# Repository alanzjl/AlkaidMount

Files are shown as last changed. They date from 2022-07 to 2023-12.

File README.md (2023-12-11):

# Alkaid Mount - DIY Equatorial Mount with HarmonicDrive

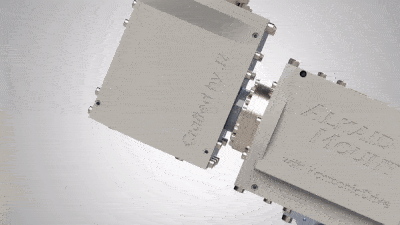
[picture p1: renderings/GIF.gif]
rendering


Built by JZ.

For my build log, checkout [this page on my website](https://alanz.info/pages/alkaidmount.html).

The following YouTube video documents all the processes with no explaination:
Youtube Video (https://www.youtube.com/watch?v=k2GoMa2DpH8)

The same video can also be found on [bilibili](https://www.bilibili.com/video/BV1SR4y1X7bt/?share_source=copy_web&vd_source=4d6f936f693563e28752aadac9dd326f).

- Note: do not directly use the dxf files under the Machine/ folder.
They are for reference only and they might contain duplicated parts, because I had to make several parts more than once due to some mistakes at the beginning.
I'd recommend looking at the solidworks files first and try to understand every part, then generate your own dxf.

## Introduction
AlkaidMount is a DIY aluminum HarmonicDrive German style equatorial mount with a ~25lbs unbalanced or >70lbs balanced load capacity, with a self weight of only ~16lbs.
Each axis consists of a 100:1 HarmonicDrive gearbox, followed by a 27:1 planetary gearbox, driven by a Nema17 stepper motor.

Weight capacity is calculated with gearbox load limits as well as rigid body simulation.
Note that I have not yet done any torture tests, so those numbers are all theoratical. 
I've only tested it on the two scopes I own - an unbalanced Williams Optics GT71 setup (~15lbs) and balanced a Meade LX200 8" SCT setup (~25lbs not including the counterweights).
Both setups worked beautifully.

This repo contains ALL the design files (CAD, manufacture drawings, PCB files, software) to make the AlkaidMount.
I made this repo public to inspire other ideas.
Due to the difficulty in sourcing the exact same model of the two HarmonicDrive's (unless you buy new:), replicating the exact same mount would be hard. 
However modifying this design to suite other HD models shouldn't be too hard.

## BOM - Hardware
-----------
| Name | Quantity | Drawings | Datasheet |
| --- | --- | --- | --- |
| Harmonic Drive CSF-17-100-2UH-LW | 2 | [Drawings](https://www.harmonicdrive.net/_hd/content/caddownloads/dxf/csf-2uh_gearheads/csf-17-xx-2uh.pdf) | [Datasheet](https://www.harmonicdrive.net/products/gear-units/gear-units/csf-2uh/csf-17-100-2uh) |
| Nema 17 with 27:1 Planetary Gearbox | 2 | [Drawings](https://www.omc-stepperonline.com/download/17HS19-1684S-PG27.pdf) | [Datasheet](https://www.omc-stepperonline.com/nema-17-stepper-motor-bipolar-l-48mm-w-gear-ratio-27-1-planetary-gearbox-17hs19-1684s-pg27) |
| 1/8" Aluminum plate | 12"x12" minimum | - | - |
| 1/4" Aluminum plate | - | - | - |
| M4x8 | many :) | - | - |
| M3x8 | not that many :] | - | - |
| M5x8 | a few :{ | - | - |

## BOM - Electronics
-----------
| Name | Quantity | Drawings | Datasheet |
| --- | --- | --- | --- |
| Teensy 4.0 | 1 | - | - |
| ESP-32 (for wifi control) | 1 | - | - |

For parts on the PCB, see [PCB/parts.txt](PCB/parts.txt).

## Manufacturing guide

Most parts were made with 2D waterjetting, with not too much post-processing (tab removal, tapping if needed).
Some parts have holes on the side, so some milling was involved.

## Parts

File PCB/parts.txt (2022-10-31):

Partlist

Exported from untitled.sch at 10/31/2022 12:25 AM

EAGLE Version 9.6.2 Copyright (c) 1988-2020 Autodesk, Inc.

Assembly variant: 

Part     Value          Device                             Package                                   Library                            Sheet

5V_REG   TSR_5V         TSR_5V                             TSR_5V                                    alans_lbr                          1
AUX3                    PINHD-1X2                          1X02                                      pinhead                            1
AUX4                    PINHD-1X2                          1X02                                      pinhead                            1
C1       0.33uF         C-EU050-024X044                    C050-024X044                              rcl                                1
C2       100uF          CPOL-EUE5-8.5                      E5-8,5                                    rcl                                1
C3       0.1uF          C-EU050-024X044                    C050-024X044                              rcl                                1
C4       47uF           CPOL-EUE5-8.5                      E5-8,5                                    rcl                                1
C5       0.1uF          C-EU050-024X044                    C050-024X044                              rcl                                1
C6       47uF           CPOL-EUE5-8.5                      E5-8,5                                    rcl                                1
C7       100uF          CPOL-EUE5-8.5                      E5-8,5                                    rcl                                1
D1       1N4004         1N4004                             DO41-10                                   adafruit                           1
FUSE1    5X20MM_FUSE    5X20MM_FUSE                        5X20MM_FUSE                               alans_lbr                          1
HND      RJ11-4X        RJ11-4X                            RJ11-NO_SHIELD                            con-tycoelectronics                1
HND_5V                  PINHD-1X2                          1X02                                      pinhead                            1
J1                      DCJ0303                            DCJ0303                                   con-jack                           1
LED1                    LED5MM                             LED5MM                                    adafruit                           1
LED2                    LED5MM                             LED5MM                                    adafruit                           1
LED3                    LED5MM                             LED5MM                                    adafruit                           1
PEC                     PINHD-1X2                          1X02                                      pinhead                            1
R1       4.7k           R-EU_0207/7                        0207/7                                    rcl                                1
R2       2k             R-EU_0207/7                        0207/7                                    rcl                                1
R3       2k             R-EU_0207/7                        0207/7                                    rcl                                1
R4       2k             R-EU_0207/7                        0207/7                                    rcl                                1
R5       2k             R-EU_0207/7                        0207/7                                    rcl                                1
R6       3.3k           R-EU_0207/7                        0207/7                                    rcl                                1
R7       3.3k           R-EU_0207/7                        0207/7                                    rcl                                1
R8       10k            R-EU_0207/7                        0207/7                                    rcl                                1
R9       10k            R-EU_0207/7                        0207/7                                    rcl                                1
R10      10k            R-EU_0207/7                        0207/7                                    rcl                                1
SWITCH   1X2-3.5MM      1X2-3.5MM                          1X2-3.5MM                                 adafruit                           1
U$1      TEENSY_4.0     TEENSY_4.0                         TEENSY_4.0                                TEENSY 4.0                         1
U1       A4988 etc      A4988_STEPPER_MOTOR_DRIVER_CARRIER MODULE_A4988_STEPPER_MOTOR_DRIVER_CARRIER A4988_STEPPER_MOTOR_DRIVER_CARRIER 1
U2       A4988 etc      A4988_STEPPER_MOTOR_DRIVER_CARRIER MODULE_A4988_STEPPER_MOTOR_DRIVER_CARRIER A4988_STEPPER_MOTOR_DRIVER_CARRIER 1
USB1     USB-B_SOCKET   USB-B_SOCKET                       USB-B_SOCKET                              alans_lbr                          1
X1       USB            JST-XH-04-PIN-ROUND-PAD            JST-XH-04-PACKAGE-ROUND-PAD               JST_XH_Connectors                  1
X2       Axis1          JST-XH-04-PIN-LONG-PAD             JST-XH-04-PACKAGE-LONG-PAD                JST_XH_Connectors                  1
X3       Axis2          JST-XH-04-PIN-LONG-PAD             JST-XH-04-PACKAGE-LONG-PAD                JST_XH_Connectors                  1
X4       WIFI           JST-XH-04-PIN-LONG-PAD             JST-XH-04-PACKAGE-LONG-PAD                JST_XH_Connectors                  1

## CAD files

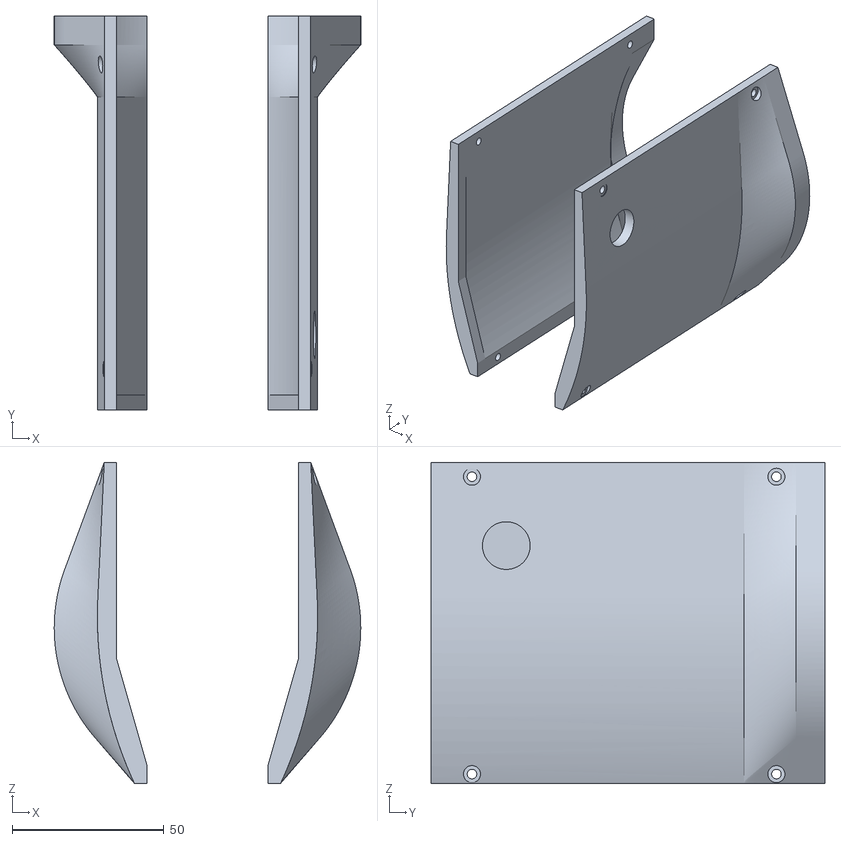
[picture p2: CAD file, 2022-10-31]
CAD/DEC/Part1^DEC_asm.STL
101.0 x 129.8 x 105.9

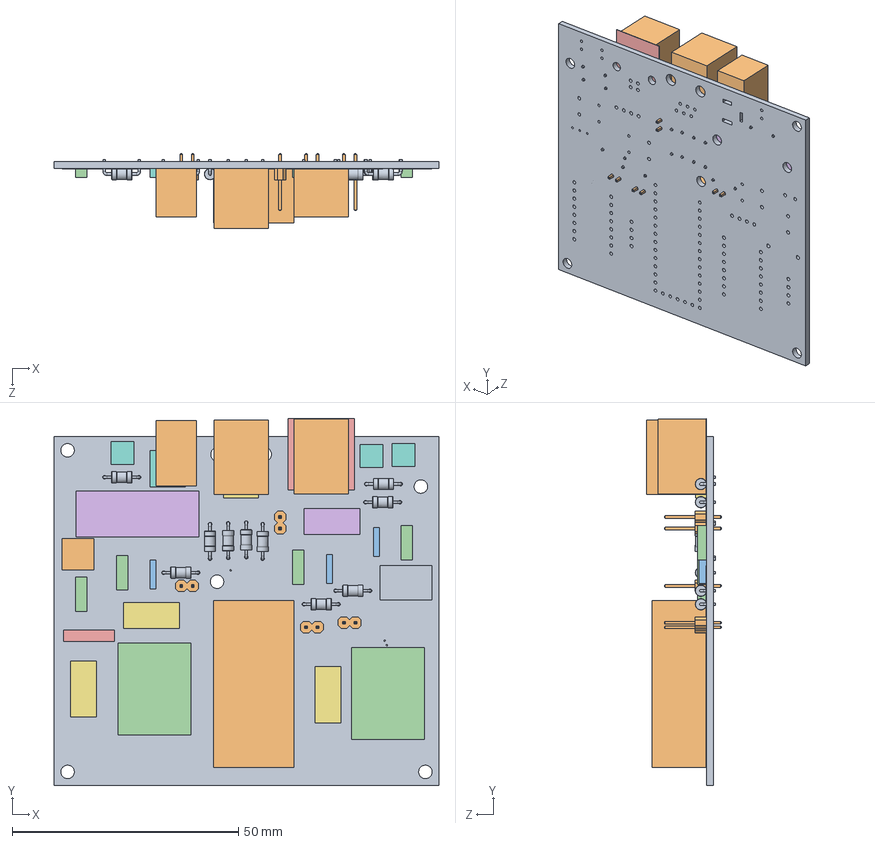
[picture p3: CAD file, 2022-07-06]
CAD/PCB/PCB.SLDASM
85.0 x 81.0 x 16.6 mm
Board.step
1X02.step x 4
0.1uF.step x 3
100uF.step x 4
1N4004.step
5X20MM_FUSE.step
RJ11-4X.step
LED5MM.step x 3
10k.step x 10
1X2-3.5MM.step
TEENSY_4.0.step
A4988 etc.step x 2
USB-B_SOCKET.step
USB.step
WIFI.step x 3
DCJ0303.step
TSR_5V.step
Part37^PCB

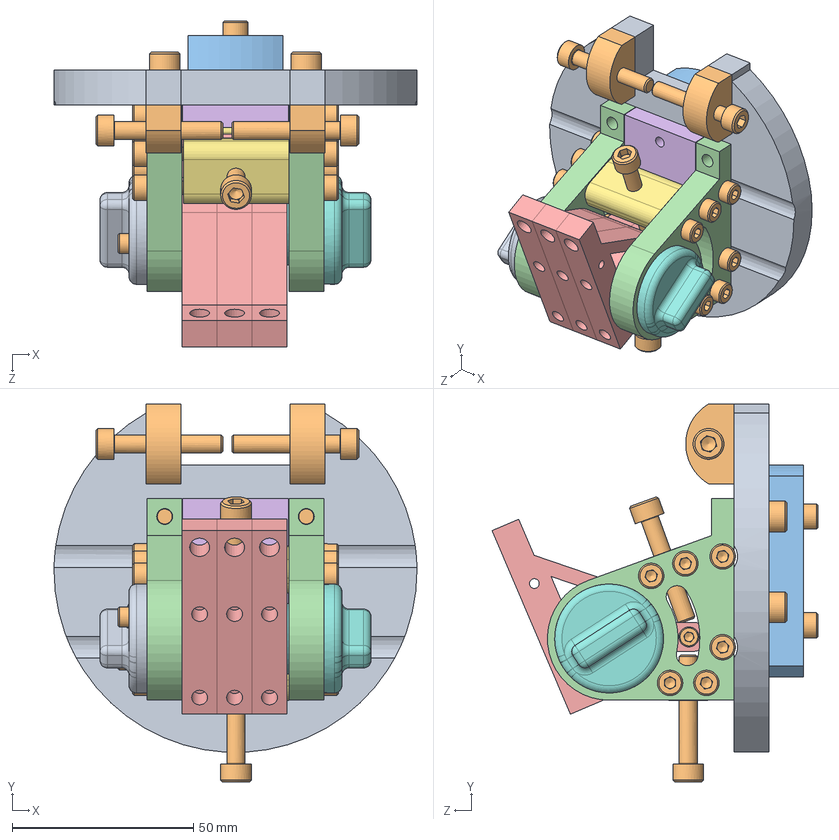
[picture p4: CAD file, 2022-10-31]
CAD/Tangent/tangent_asm.SLDASM
100.0 x 104.1 x 89.8 mm
tangent_base
tangent_az x 2
tangent_tripod_spacer
tangent_alt x 2
tangent_mount x 3
tangent_alt_spacer
alt_bolt_housing x 2
alt_locker_base
alt_locker_cap
socket head cap screw_am x 26
socket countersunk head screw_am x 4

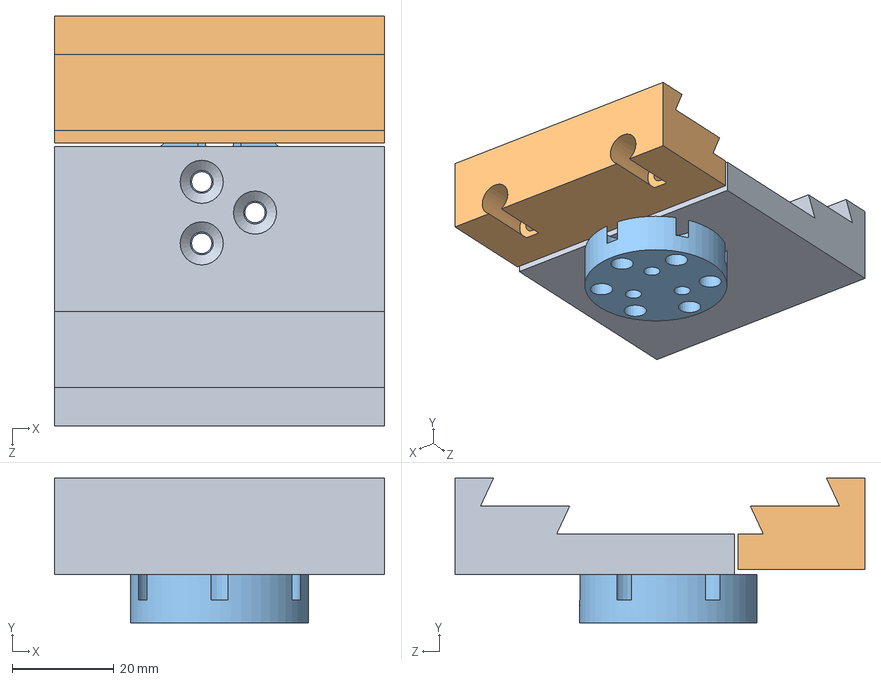
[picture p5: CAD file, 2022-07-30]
CAD/Dovetail/Dovetail_asm.SLDASM
65.0 x 28.5 x 80.7 mm
clamp_main
clamp_side
connector

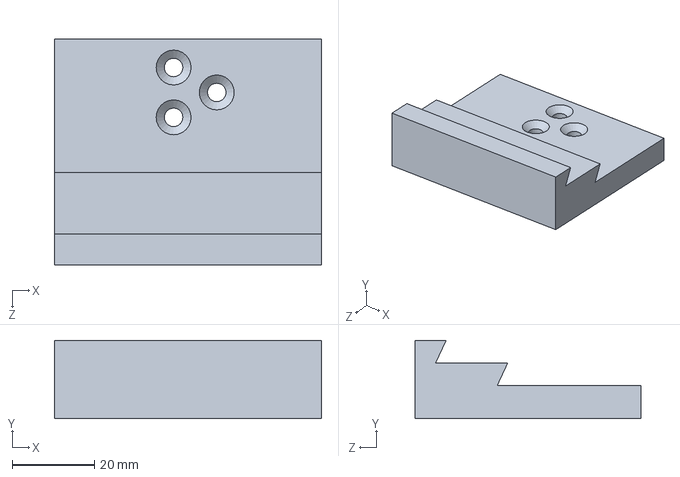
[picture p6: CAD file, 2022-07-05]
CAD/Dovetail/clamp_main.SLDPRT
65.0 x 19.0 x 55.0 mm

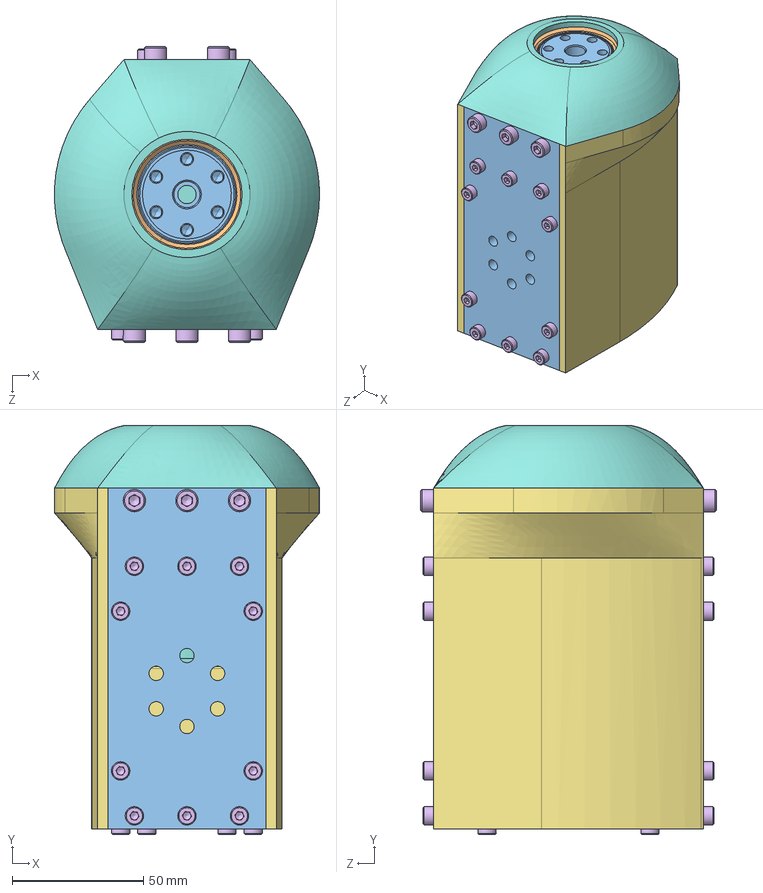
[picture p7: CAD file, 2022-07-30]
CAD/DEC/DEC_asm.SLDASM
100.9 x 155.7 x 112.7 mm
DEC_gearbox_mount
CSF-17-2UH HOUSING.stp
CSF-17-2UH OUTPUT.stp
CSF-17-2A-R OLDHAM COUPLING.stp
1715063_1715063.stp x 2
17 WG BEARING.stp
6627T91_Stepper Motor
Planatary_Gearbox_27_1
DEC_planetary_mount
DEC_top_plate
DEC_bottom_plate
DEC_middle_support_v2
support_triangle x 8
socket head cap screw_am x 33

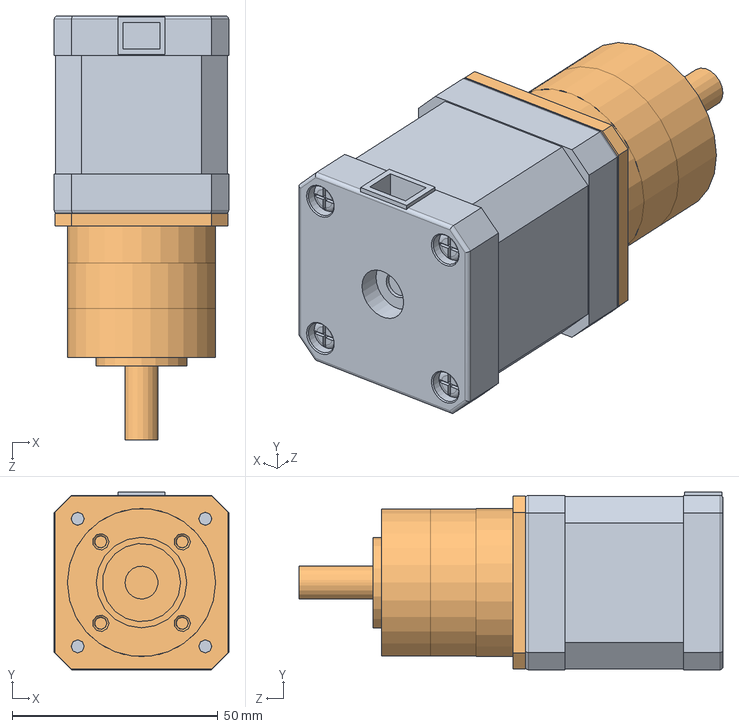
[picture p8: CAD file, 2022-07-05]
CAD/parts/Nema17_27_1.SLDASM
42.4 x 43.2 x 103.0 mm
6627T91_Stepper Motor
Planatary_Gearbox_27_1

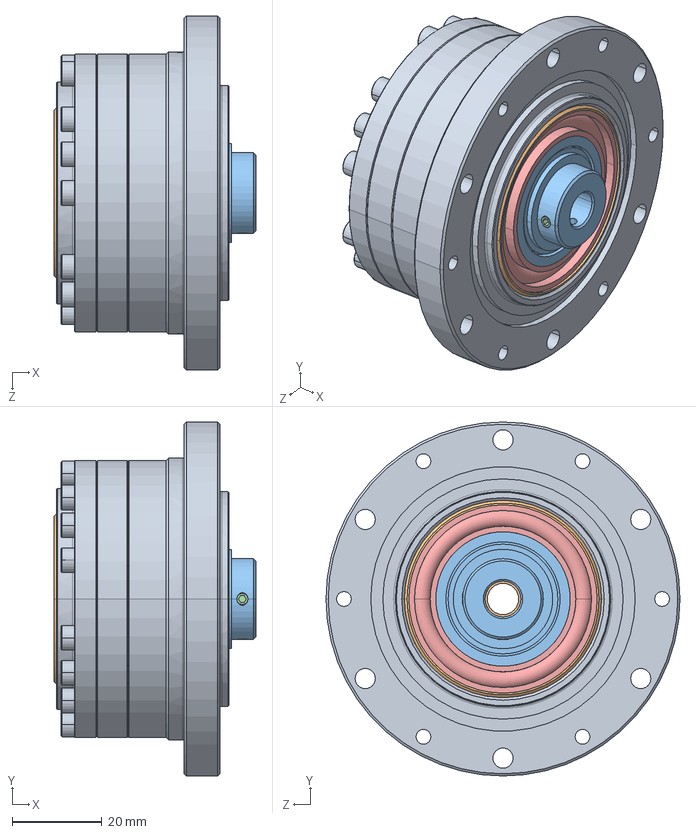
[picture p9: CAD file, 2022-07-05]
CAD/parts/CSF-17-XXX-2UH.stp.SLDASM
45.0 x 79.0 x 79.0 mm
CSF-17-2UH HOUSING.stp
CSF-17-2UH OUTPUT.stp
CSF-17-2A-R OLDHAM COUPLING.stp
1715063_1715063.stp x 2
17 WG BEARING.stp

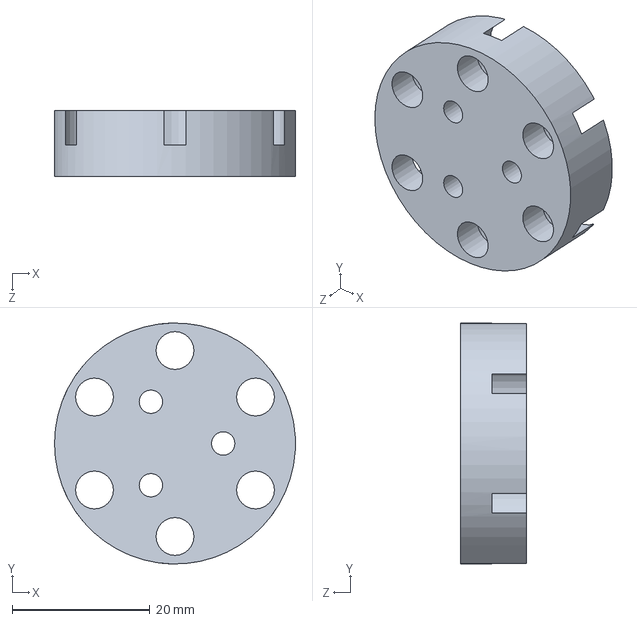
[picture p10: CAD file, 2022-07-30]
CAD/Dovetail/connector.SLDPRT
35.0 x 35.0 x 9.53 mm

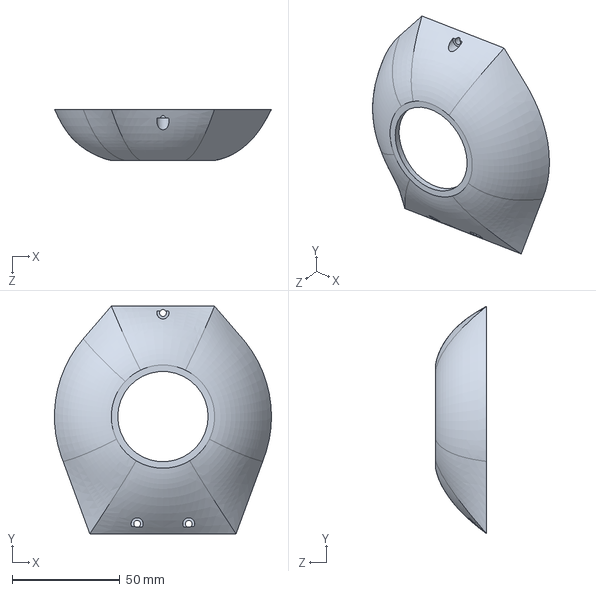
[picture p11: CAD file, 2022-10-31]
CAD/output_cap.SLDPRT
100.9 x 105.9 x 23.8 mm

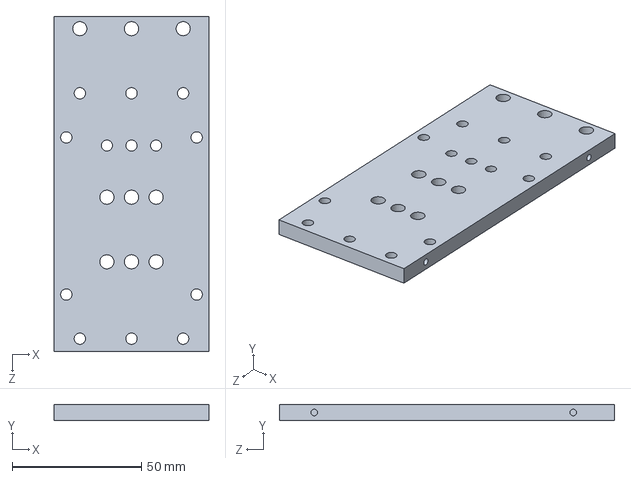
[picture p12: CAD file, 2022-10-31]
CAD/RA/RA_bottom_plate.SLDPRT
60.0 x 6.35 x 129.8 mm

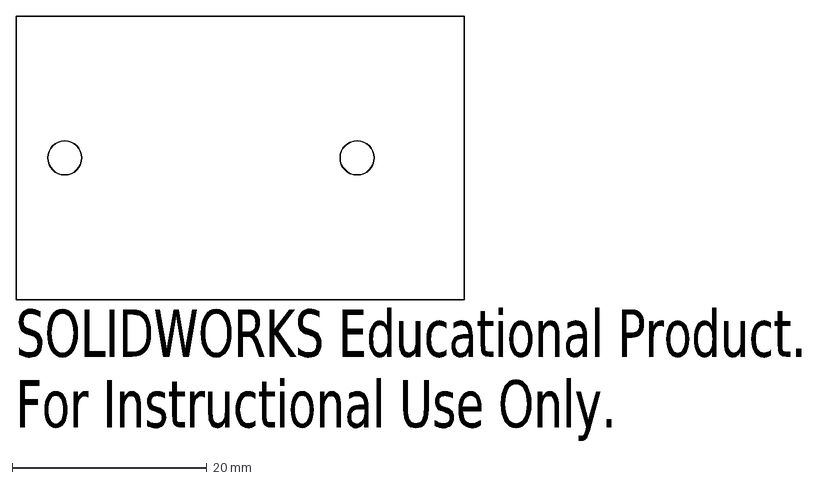
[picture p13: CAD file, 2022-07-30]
Machine/dxf/1_4_inch/1_x_tangent_alt_spacer.DXF
SOLIDWORKS Educational Product.
For Instructional Use Only.

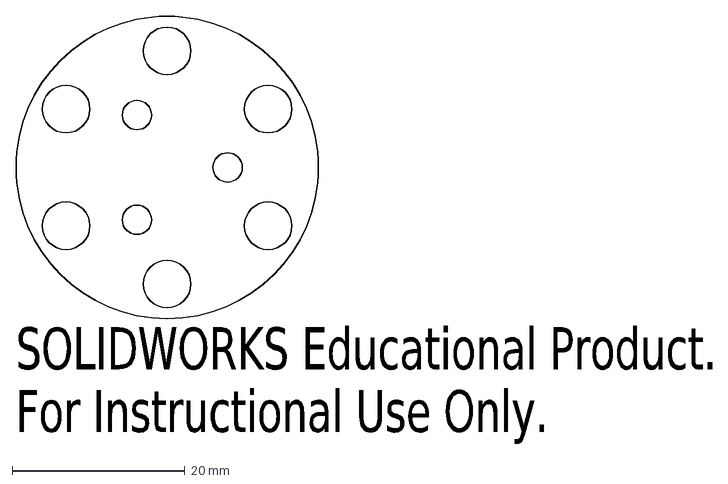
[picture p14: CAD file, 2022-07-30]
Machine/dxf/3_8_inch/1_x_connector.DXF
SOLIDWORKS Educational Product.
For Instructional Use Only.

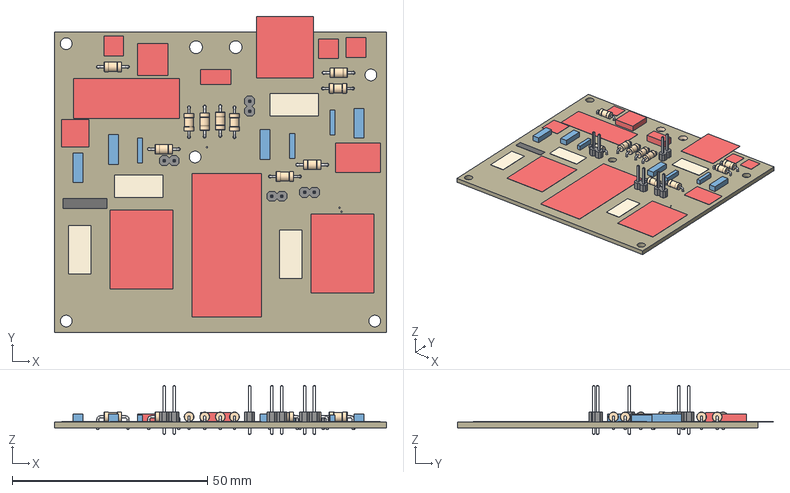
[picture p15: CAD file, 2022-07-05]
CAD/PCB/untitled(2).step
85.0 x 81.0 x 12.6 mm
Board
1X02 x 4
0.1uF x 3
100uF x 4
1N4004
5X20MM_FUSE
RJ11-4X
LED5MM x 3
10k x 10
1X2-3.5MM
TEENSY_4.0
A4988 etc x 2
USB-B_SOCKET
USB
WIFI x 3
DCJ0303
TSR_5V

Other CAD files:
CAD/RA/Part1^DEC_asm.STL
CAD/DEC/output_cap.STL
CAD/parts/CSF-17-2UH OUTPUT.stp.SLDPRT
CAD/RA/RA_shell_right.SLDPRT
CAD/DEC/DEC_bottom_plate.SLDPRT
CAD/DEC/DEC_gearbox_mount.SLDPRT
CAD/DEC/DEC_middle_support.SLDPRT
CAD/DEC/DEC_middle_support_v2.SLDPRT
CAD/DEC/DEC_planetary_mount.SLDPRT
CAD/DEC/DEC_shell_left.STL
CAD/DEC/DEC_shell_right.STL
CAD/DEC/DEC_top_plate.SLDPRT
CAD/DEC/cw_tube_housing.SLDPRT
CAD/Dovetail/clamp_side.SLDPRT
CAD/RA/RA.SLDDRW
CAD/RA/RA_gearbox_mount.SLDDRW
CAD/RA/RA_gearbox_mount.SLDPRT
CAD/RA/RA_middle_support.SLDDRW
CAD/RA/RA_middle_support.SLDPRT
CAD/RA/RA_planetary_mount.SLDPRT
CAD/RA/RA_shell_left.SLDPRT
CAD/RA/RA_shell_left.STL
CAD/RA/RA_shell_right.STL
CAD/RA/RA_top_plate.SLDPRT
CAD/RA/output_extension.SLDPRT
CAD/Tangent/alt_bolt_housing.SLDPRT
CAD/Tangent/alt_locker_base.SLDPRT
CAD/Tangent/alt_locker_cap.SLDPRT
CAD/Tangent/tangent_alt.SLDDRW
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

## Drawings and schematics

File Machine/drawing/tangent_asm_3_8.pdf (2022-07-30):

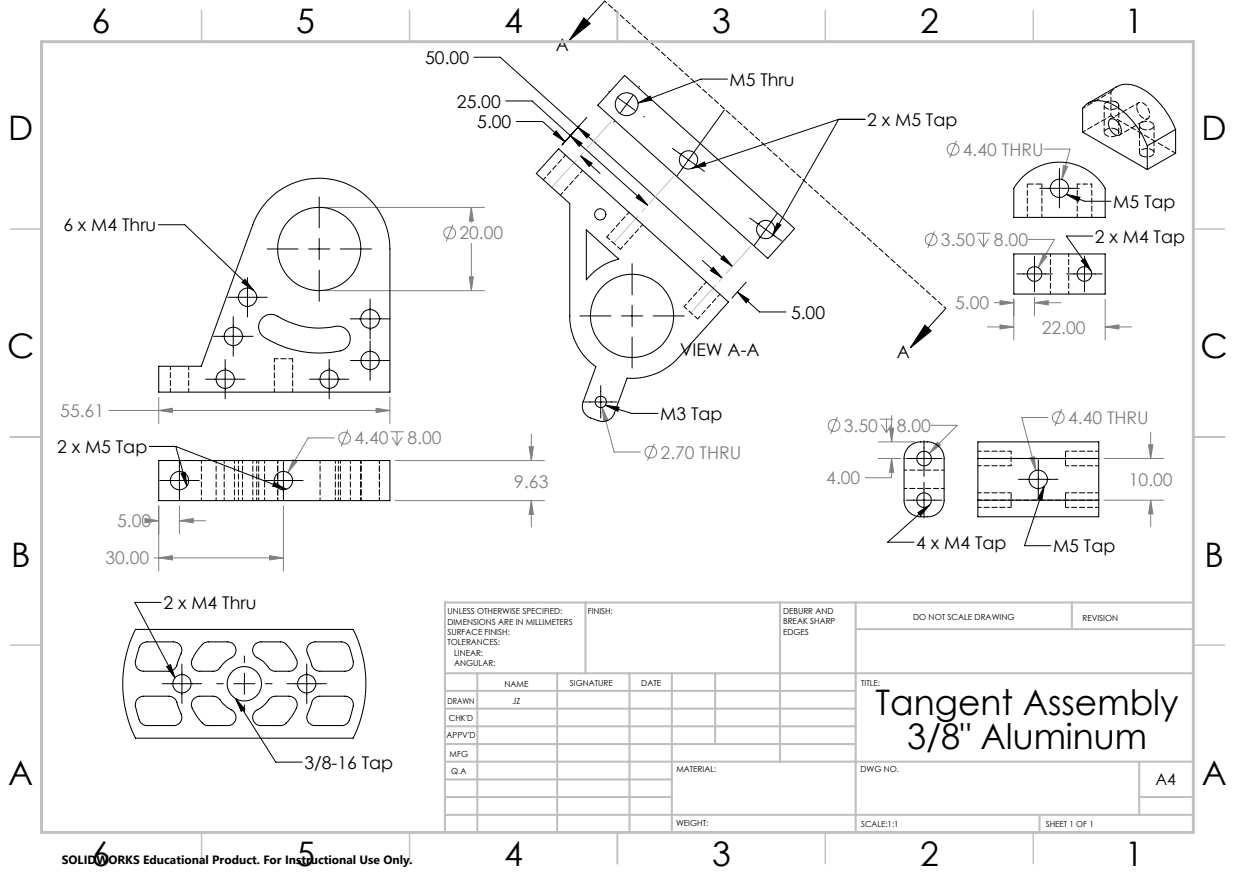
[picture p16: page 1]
20.00 6 x M4 Thru; 2 x M5 Tap; 2.70 THRU; M3 Tap; VIEW A-A; M5 Thru; 4.40 THRU; M5 Tap; 4 x M4 Tap; 2 x M4 Tap; 2 x M4 Thru; 3/8-16 Tap A; FINISH:; DEBURR AND; BREAK SHARP; DO NOT SCALE DRAWING; REVISION; SCALE:1:1; SHEET 1 OF 1

UNLESS OTHERWISE SPECIFIED:
DIMENSIONS ARE IN MILLIMETERS
SURFACE FINISH:
TOLERANCES:
LINEAR:
ANGULAR:

DRAWN | JZ

NAME | SIGNATURE | DATE | | | | TITLE: Tangent Assembly 3/8" Aluminum

CHK'D
APPV'D
MFG
Q.A | | | | MATERIAL: | DWG NO. | A4

SOLIDWORKS Educational Product. For Instructional Use Only.

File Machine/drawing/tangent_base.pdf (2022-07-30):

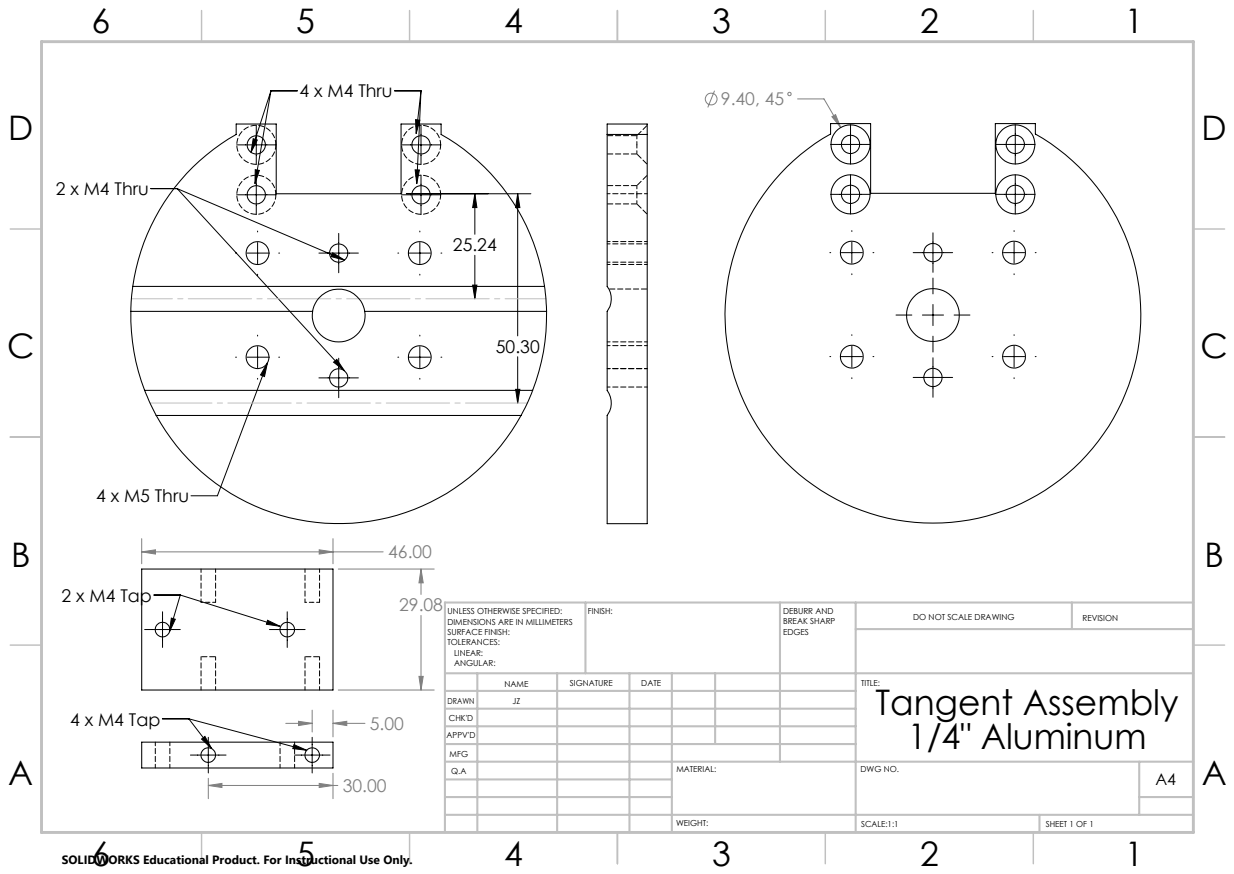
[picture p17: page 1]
4 x M4 Thru; 2 x M4 Thru; 4 x M5 Thru; 29.08 2 x M4 Tap; FINISH:; DEBURR AND; BREAK SHARP; DO NOT SCALE DRAWING; REVISION; SCALE:1:1; SHEET 1 OF 1

UNLESS OTHERWISE SPECIFIED:
DIMENSIONS ARE IN MILLIMETERS
SURFACE FINISH:
TOLERANCES:
LINEAR:
ANGULAR:

DRAWN | JZ

NAME | SIGNATURE | DATE | | | | TITLE: Tangent Assembly 1/4" Aluminum

4 x M4 Tap
SOLIDWORKS Educational Product. For Instructional Use Only.

CHK'D
APPV'D
MFG
Q.A | | | | MATERIAL: | DWG NO. | A4

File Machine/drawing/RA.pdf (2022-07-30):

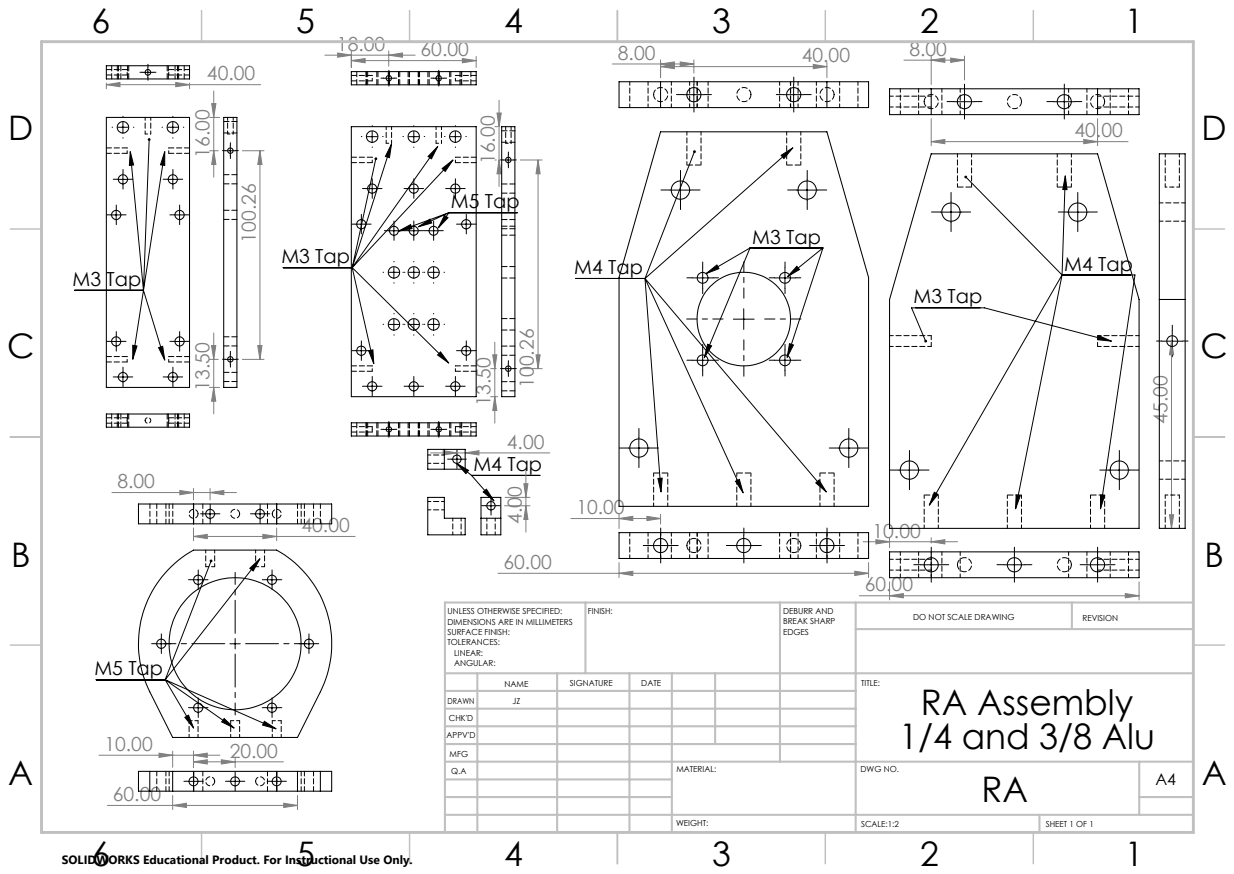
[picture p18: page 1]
M3 Tap; M5 Tap; M4 Tap; 4.00 4.00 M4 Tap; FINISH:; DEBURR AND; BREAK SHARP; DO NOT SCALE DRAWING; REVISION; SCALE:1:2; SHEET 1 OF 1

UNLESS OTHERWISE SPECIFIED:
DIMENSIONS ARE IN MILLIMETERS
SURFACE FINISH:
TOLERANCES:
LINEAR:
ANGULAR:

NAME | SIGNATURE | DATE | | | | TITLE: RA Assembly 1/4 and 3/8 Alu

DRAWN | JZ
CHK'D
APPV'D
MFG
Q.A | | | | MATERIAL: | DWG NO. RA | A4

SOLIDWORKS Educational Product. For Instructional Use Only.

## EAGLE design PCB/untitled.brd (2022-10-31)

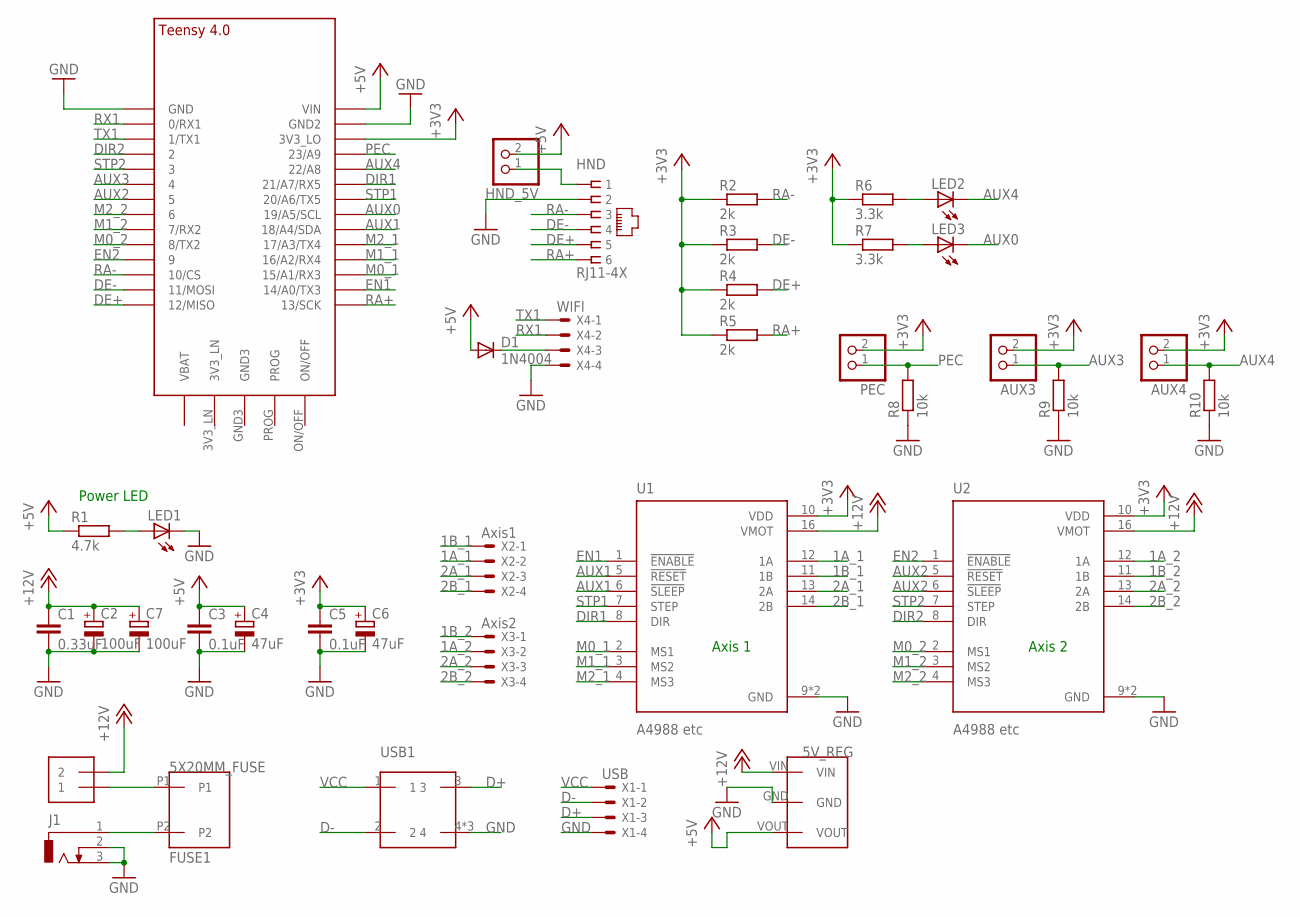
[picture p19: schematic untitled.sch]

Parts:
5V_REG: TSR_5V
AUX3, AUX4: PINHD-1X2; 1X02
C1: 0.33uF; C050-024X044
C2, C7: 100uF; E5-8,5
C3, C5: 0.1uF; C050-024X044
C4, C6: 47uF; E5-8,5
D1: 1N4004; DO41-10
FUSE1: 5X20MM_FUSE
HND: RJ11-4X; RJ11-NO_SHIELD
HND_5V: PINHD-1X2; 1X02
J1: DCJ0303
LED1, LED2, LED3: LED5MM
PEC: PINHD-1X2; 1X02
R1: 4.7k; 0207/7
R2, R3, R4, R5: 2k; 0207/7
R6, R7: 3.3k; 0207/7
R8, R9, R10: 10k; 0207/7
SWITCH: 1X2-3.5MM
U1, U2: A4988 etc; MODULE_A4988_STEPPER_MOTOR_DRIVER_CARRIER
U$1: TEENSY_4.0
USB1: USB-B_SOCKET
X1: USB; JST-XH-04-PACKAGE-ROUND-PAD
X2: Axis1; JST-XH-04-PACKAGE-LONG-PAD
X3: Axis2; JST-XH-04-PACKAGE-LONG-PAD
X4: WIFI; JST-XH-04-PACKAGE-LONG-PAD

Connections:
1A_1: U1.12 (1A), X2.2
1A_2: U2.12 (1A), X3.2
1B_1: U1.11 (1B), X2.1
1B_2: U2.11 (1B), X3.1
2A_1: U1.13 (2A), X2.3
2A_2: U2.13 (2A), X3.3
2B_1: U1.14 (2B), X2.4
2B_2: U2.14 (2B), X3.4
+3V3: AUX3.2, AUX4.2, C5.1, C6.+, PEC.2, R2.1, R3.1, R4.1, R5.1, R6.1, R7.1, U1.10 (VDD), U2.10 (VDD), U$1.3V3_LO
+5V: 5V_REG.VOUT, C3.1, C4.+, D1.A, HND_5V.2, R1.1, U$1.VIN
+12V: 5V_REG.VIN, C1.1, C2.+, C7.+, SWITCH.2, U1.16 (VMOT), U2.16 (VMOT)
AUX0: LED3.K (C), U$1.19/A5/SCL
AUX1: U1.5 (!RESET), U1.6 (!SLEEP), U$1.18/A4/SDA
AUX2: U2.5 (!RESET), U2.6 (!SLEEP), U$1.5
AUX3: AUX3.1, R9.2, U$1.4/CANRX (4)
AUX4: AUX4.1, LED2.K (C), R10.2, U$1.22/A8
D+: USB1.3, X1.3
D-: USB1.2, X1.2
DE+: HND.5, R4.2, U$1.12/MISO
DE-: HND.4, R3.2, U$1.11/MOSI
DIR1: U1.8 (DIR), U$1.21/A7 (21/A7/RX5)
DIR2: U2.8 (DIR), U$1.2
EN1: U1.1 (!ENABLE), U$1.14/A0 (14/A0/TX3)
EN2: U2.1 (!ENABLE), U$1.9/CS (9)
GND: 5V_REG.GND, C1.2, C2.-, C3.2, C4.-, C5.2, C6.-, C7.-, HND.2, J1.2, J1.3, LED1.K (C), R8.1, R9.1, R10.1, U1.9 (GND), U1.15 (GND), U2.9 (GND), U2.15 (GND), U$1.GND, U$1.GND2, USB1.4, USB1.P$1 (4), USB1.P$2 (4), X1.4, X4.4
M0_1: U1.2 (MS1), U$1.15/A1 (15/A1/RX3)
M0_2: U2.2 (MS1), U$1.8 (8/TX2)
M1_1: U1.3 (MS2), U$1.16/A2 (16/A2/RX4)
M1_2: U2.3 (MS2), U$1.7 (7/RX2)
M2_1: U1.4 (MS3), U$1.17/A3 (17/A3/TX4)
M2_2: U2.4 (MS3), U$1.6
unnamed: FUSE1.P2, J1.1
unnamed: FUSE1.P1, SWITCH.1
unnamed: LED1.A, R1.2
unnamed: D1.C, X4.3
unnamed: HND.1, HND_5V.1
unnamed: LED2.A, R6.2
unnamed: LED3.A, R7.2
PEC: PEC.1, R8.2, U$1.23/A9
RA+: HND.6, R5.2, U$1.13/SCK
RA-: HND.3, R2.2, U$1.10/CS
RX1: U$1.0/RX (0/RX1), X4.2
STP1: U1.7 (STEP), U$1.20/A6 (20/A6/TX5)
STP2: U2.7 (STEP), U$1.3/CANTX (3)
TX1: U$1.1/TX (1/TX1), X4.1
VCC: USB1.1, X1.1

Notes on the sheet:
Power LED
Axis 1
Axis 2

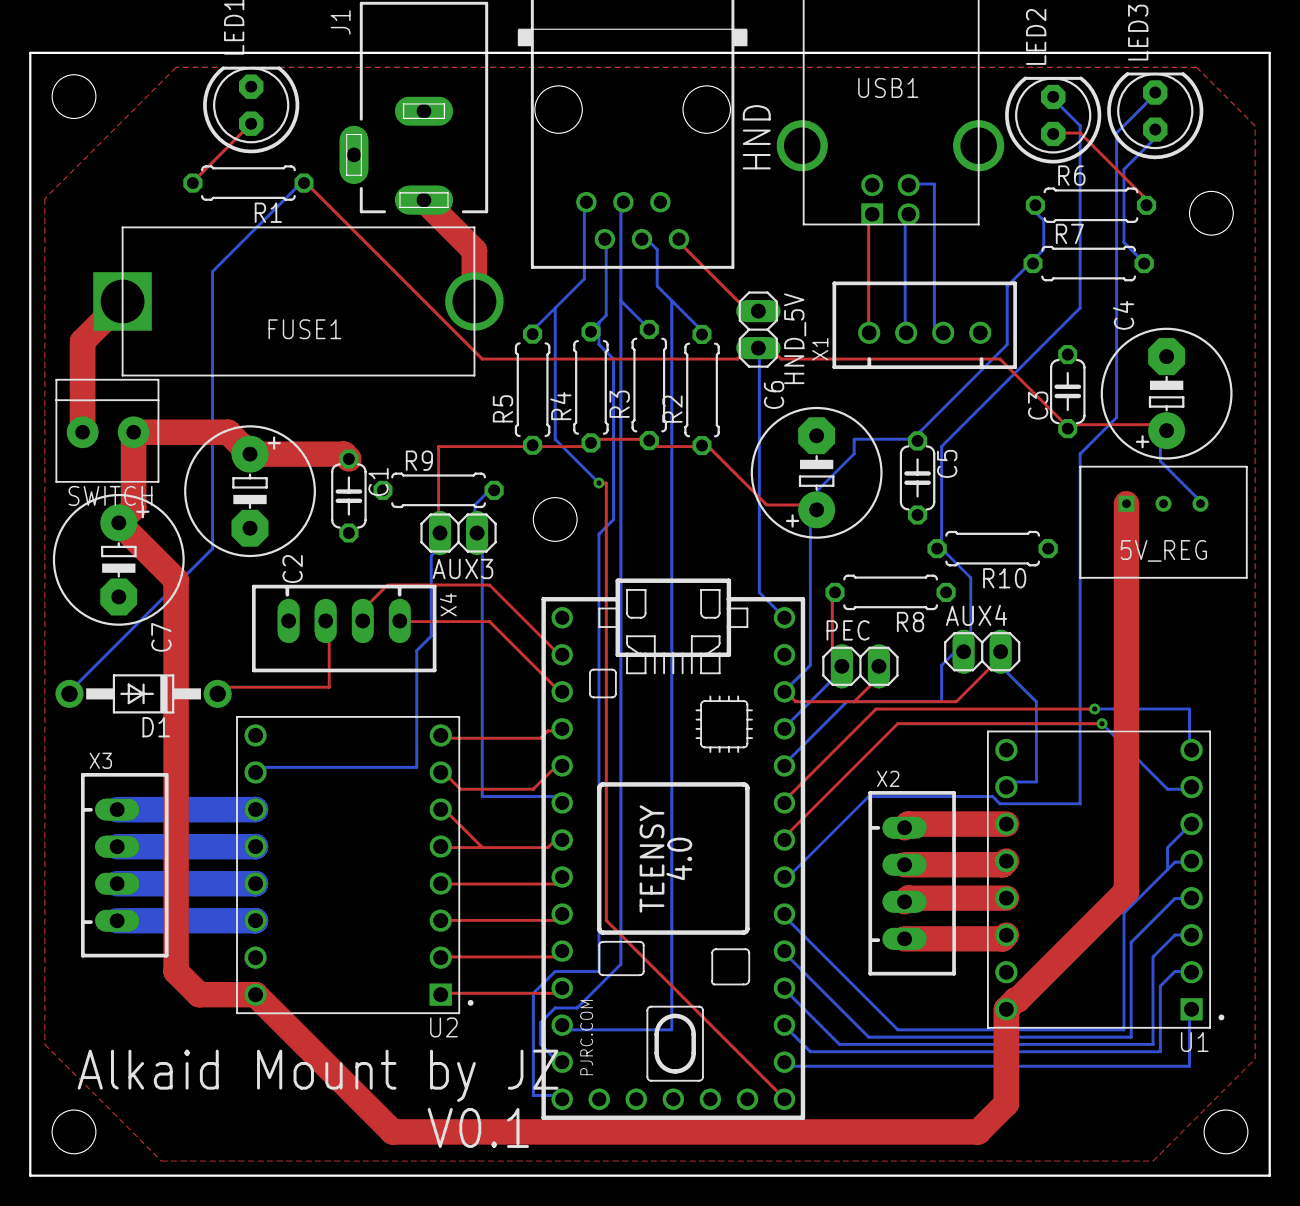
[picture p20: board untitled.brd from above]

Board: 2 copper layers, 85.0 x 78.6 mm, 38 parts (0 on the bottom side), 46 nets.

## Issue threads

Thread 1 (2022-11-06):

Zip file for all cad files

masydoblig, 2022-11-06:
Hi

Absolutely love this. Great Work im super impressed and loved the you tube video. a video on how the system works would be a great update.

I have been thinking of making the same thing in Solidworks for months.

Do you have a zip file for all the cad Files? i Cant seem to find it if there is one? Also im not used to git hub

Also with the controller board is there a schematic somewhere?

alanzjl, 2022-11-08:
Hi,

you can download the whole repo as a .zip file. The CAD folder contains all the SolidWorks source files. The PCB folder has the PCB schematic, board design, as well as the CAM files - meaning you can edit them in eagle or just send the CAM files directly to a PCB manufacturer. I’ll close this issue as it’s not something that needs to be fixed. But I’m happy to answer other questions.

Thanks

Closed 2022-11-08.

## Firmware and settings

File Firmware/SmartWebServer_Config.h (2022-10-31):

// ---------------------------------------------------------------------------------------------------------------------------------
// Configuration for OnStep SmartWebServer Add-on

/*
 *               For more information on setting this addon up see https://onstep.groups.io/g/main/wiki/7119 
 *                           and join the OnStep Groups.io at https://groups.io/g/onstep
 * 
 *           *** Read the compiler warnings and errors, they are there to help guard against invalid configurations ***
*/

// ---------------------------------------------------------------------------------------------------------------------------------
// ADJUST THE FOLLOWING TO CONFIGURE YOUR ADD-ON'S FEATURES ------------------------------------------------------------------------
// <-Req'd = always must set, <-Often = usually must set, Option = optional, Adjust = adjust as req'd, Infreq = infrequently changed

// For Wifi successful startup an AP will appear with an SSID of "ONSTEP", after connecting: the web-site is at "192.168.0.1" and
// the cmd channel is at "192.168.0.1:9999". If locked out selecting "Erase Flash: All Flash Contents" from the Arduino Tools menu 
// before uploading/flashing again can help restore access to the ESP8266.

//      Parameter Name              Value   Default  Notes                                                                      Hint
// OPERATIONAL MODE ----------------------------------------------------------------------------------------------------------------
#define OPERATIONAL_MODE             WIFI //   WIFI, Or use ETHERNET_W5100 or ETHERNET_W5500                                  Adjust

// SERIAL PORTS --------------------------------------------------------------------------------------------------------------------
#define SERIAL_BAUD_DEFAULT          9600 //   9600, Common baud rates for this parameter are 9600,19200,57600,115200,etc.    Infreq
                                          //         The OnStep serial port this is wired to must use the same rate above.
#define SERIAL_BAUD                 57600 //  57600, Or use 19200,57600,115200. For 230400,460800 set all three to the same rate
                                          //         (OnStep and here.)  Automatically uses 19200 if talking to a Mega2560 OnStep.
#define SERIAL_SWAP                  AUTO //   AUTO, Automatic check both, ON for swapped port or OFF for default port only.  Infreq
                                          //         this option is ignored in ETHERNET modes

// STATUS LED ----------------------------------------------------------------------------------------------------------------------
#define LED_STATUS                     ON //     ON, Enable LED flashes while connecting then steady once connected.          Infreq

// DISPLAY -------------------------------------------------------------------------------------------------------------------------
#define DISPLAY_LANGUAGE             L_en //   L_en, English. Specify language with two letter country code, if supported.    Adjust
#define DISPLAY_WEATHER               OFF //    OFF, ON ambient conditions in locale default units.                           Option
#define DISPLAY_INTERNAL_TEMPERATURE  OFF //    OFF, ON internal MCU temp. in locale default units.                           Option
#define DISPLAY_WIFI_SIGNAL_STRENGTH   ON //     ON, Wireless signal strength reported via web interface. OFF otherwise.      Option
#define DISPLAY_RESET_CONTROLS        OFF //    OFF, ON to allow reset of OnStep, FWU for STM32 firmware upload pin HIGH.     Option

#define DISPLAY_SPECIAL_CHARS          ON //     ON, For standard ASCII special symbols (compatibility.)                      Infreq
#define DISPLAY_ADVANCED_CHARS         ON //     ON, For standard "RA/Dec" instead of symbols.                                Infreq
#define DISPLAY_HIGH_PRECISION_COORDS OFF //    OFF, ON for high precision coordinate display on status page.                 Infreq

// DRIVE CONFIGURATION -------------------------------------------------------------------------------------------------------------
#define DRIVE_CONFIGURATION            ON //    ON, to display/modify mount, rotator, focuser settings                        Option
#define DRIVE_MAIN_AXES_MICROSTEPS     ON //    ON, to display Axis1/2 Microsteps if available.                               Option
#define DRIVE_MAIN_AXES_CURRENT        ON //    ON, to display Axis1/2 IRUN if available.                                     Option
#define DRIVE_MAIN_AXES_REVERSE        ON //    ON, to display Axis1/2 Reverse if available.                                  Option
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

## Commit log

2022-07-05 finish pcb design
    [17 WG BEARING.stp.SLDPRT, 1715063_1715063.stp.SLDPRT, 5972K288_Ball Bearing.SLDPRT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]
2022-07-06 fix hole size WIP, add some drawings
    [1_x_drill_tangent_mount.DXF, 1_x_tangent_alt_spacer.DXF, 1_x_tangent_base.DXF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]
2022-07-12 update dimension for plate thickness
    [DEC_asm.SLDASM, DEC_bottom_plate.SLDPRT, DEC_middle_support.SLDPRT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]
2022-07-13 add drawings
    [tangent_alt.SLDDRW, tangent_asm.SLDASM, tangent_base.SLDDRW]
2022-07-30 add final cad
    [16_x_support_triangle.DXF, 1_4.dxf, 1_x_DEC_bottom_plate.DXF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]
2022-10-31 add readme and other stuff
    [DEC_bottom_plate.SLDPRT, DEC_shell_left.STL, DEC_shell_right.STL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]
